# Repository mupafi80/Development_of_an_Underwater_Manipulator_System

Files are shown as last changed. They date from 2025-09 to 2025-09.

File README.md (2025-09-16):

# Development_of_an_Underwater_Manipulator_System
This repository documents the development of an underwater manipulator. It includes the design methodology, material selection for mechanical construction, electronic system components, software development, and the physical assembly of the manipulator. Design files for the manipulator arm components and electrical connection diagrams are available in this repository. This project is part of the doctoral thesis of PhD Salatiel García Nava.

The proposed arm structure and link dimensions are presented below.



The components of a link in the robotic arm, including sections of tubing, flanges, and seals, are observed.



Assembled links: the first one includes the o-rings between the threaded sections, while the lower two display the connecting threads.



García Nava, Salatiel (2025). Desarrollo de un brazo manipulador subacuático. Centro de Investigación y de Estudios Avanzados del IPN. Directores de tesis: Dr. Filiberto Muñoz Palacios, Dr. Sergio Rogelio Lozano Leal. Tesis de doctorado

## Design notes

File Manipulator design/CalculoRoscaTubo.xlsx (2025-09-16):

Calculo de las medidas básicas |  |  |  |  | Sistema ISO
Para el calculo de las distintas medidas se toman como base el diámetro exterior del tornillo d y el paso de rosca P.
Las roscas de este sistema son roscas métricas y sus medidas vienen expresadas en milímetros. El ángulo de rosca es de 60º.
 |  |  |  |  |  |  |  |  | Profundidad de rosca................. H = 0,866 · P
 |  |  |  |  |  |  |  |  | Altura de contacto....................... H1 = 0,541 · P
 |  |  |  |  |  |  |  |  | Altura del filete del tornillo...........h3 = 0,613 · P
 |  |  |  |  |  |  |  |  | Diámetro interior del tornillo.......d3 = d - 1,226 · P
 |  |  |  |  |  |  |  |  | Diámetro interior de la tuerca.....D1 = d - 1,082 · P
 |  |  |  |  |  |  |  |  | Diámetro medio...........................d2 = D2 = d - 0,649 · P
 |  |  |  |  |  |  |  |  | Diámetro exterior de la tuerca....D = d + 0,072 · P
 |  |  |  |  |  |  |  |  | Cálculo de d a partir de diametro de tubo …...............d=D1-(1.082*P) donde D1 es diametro interior de la tuerca
 | Diametro Nominal : |  | 51.418 |  | Paso: | 1 |  |  | DITuerca: | 52.4 | Paso: | 1 |  |  |  | Medida de redondo para hacer cuerda | 51.49
 |  |  |  |  |  |  |  |  |  |  |  |  |  |  |  | Medida de tubo para hacer cuerda | 52.4
 | H: | 0.866 | H1: | 0.541 | h3: | 0.613 |  |  | H: | 0.866 | H/8 | 0.10825 | H1 | 0.541 | d (new) | 53.482
 | d3: | 50.192 | D1: | 50.336 | d2=D2: | 50.769 | D: | 51.49 | 2H: | 1.732 | 2 H/8: | 0.2165 | d: | 53.482
 | Diametro Nominal : |  | 9.993 |  | Paso: | 1.5 |  |  | DITuerca: | 8.37 | Paso: | 1.5 |  |  |  | Medida de redondo para hacer cuerda | 10.101
 |  |  |  |  |  |  |  |  |  |  |  |  |  |  |  | Medida de tubo para hacer cuerda | 8.37
 | H: | 1.299 | H1: | 0.8115 | h3: | 0.9195 |  |  | H: | 1.299 | H/8 | 0.162375
 | d3: | 8.154 | D1: | 8.37 | d2=D2: | 9.0195 | D: | 10.101 | 2H: | 2.598 | 2 H/8: | 0.32475 | d: | 9.993
 |  |  |  |  |  |  |  |  | D1 | 50.407468
La Norma DIN 13-1, establece las características de las roscas métricas gruesas cuyos tamaños van desde la M1 a M68. En la Tabla B, como ejemplo se especifican los valores de algunas de ellas.
Diámetro nominal: D = d
Paso: P
D1 = d – 2·H1 = d – 1,082532·P
Diámetro medio: D2 = d2 = d – 0,649519 · P
Diámetro del núcleo: d3 = d – 1,226869 · P
H = 0,866025 · P
Profundidad portante de rosca: H1 = 0,541266·P
Profundidad de rosca: h3 = 0,613435·P
Radio fondo de rosca: R = H/6 = 0,144338 · P
Las roscas ISO métricas finas se regulan por la norma DIN 13-2 a la DIN 13-11 1999-11 y diámetros nominales de 1mm a 1000 mm y pasos finos de 0,2 a 8 mm.

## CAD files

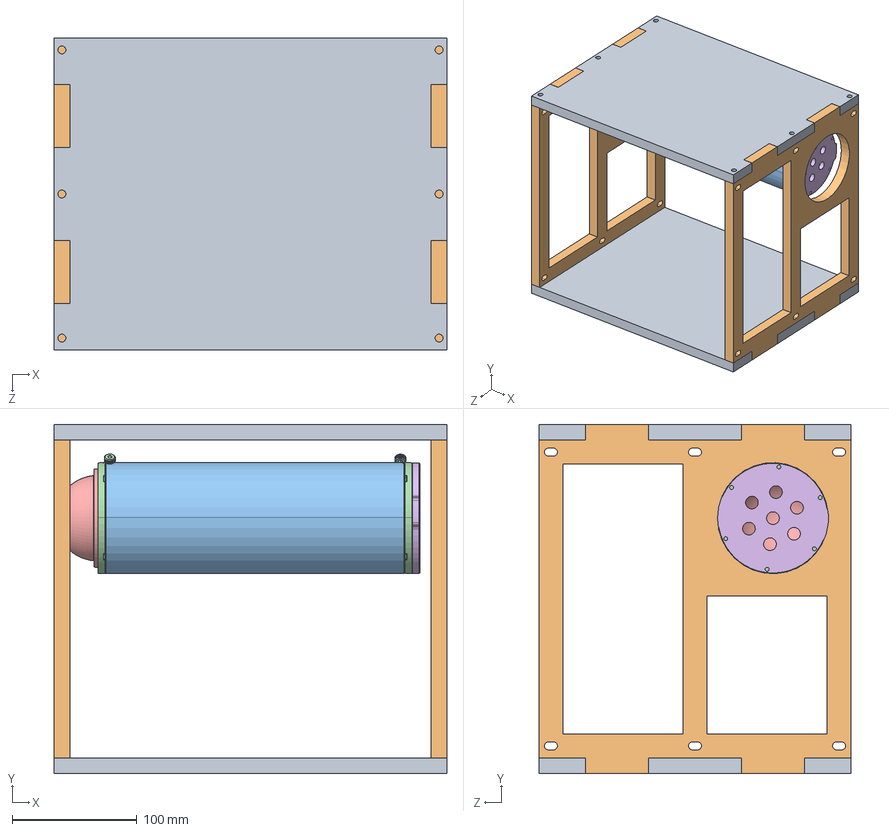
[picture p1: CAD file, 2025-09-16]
Manipulator design/EnsamblajeRobotC_Movimiento.SLDASM
315.0 x 280.0 x 250.0 mm
TP_Base x 2
Side_Base x 2
WTE3-P-LOCKING-TUBE-240-R2
WTE3-M-LOCKING-FLANGE-SEAL-R1-RP x 2
WTE3-P-DOME-R1
WTE3-M-END-CAP-7-HOLE-R1

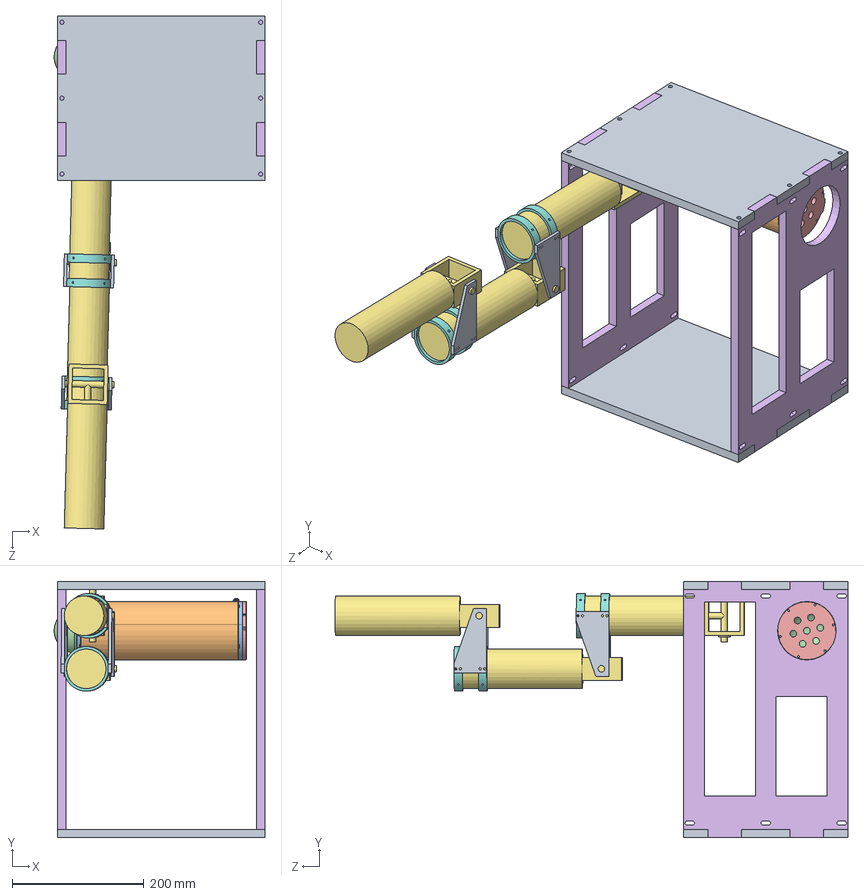
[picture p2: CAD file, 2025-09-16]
Manipulator design/EnsamblajeRobotC_Movimiento_Long.SLDASM
320.5 x 390.0 x 780.2 mm
TP_Base x 2
WTE3-P-LOCKING-TUBE-240-R2
WTE3-M-LOCKING-FLANGE-SEAL-R1-RP x 2
WTE3-P-DOME-R1
WTE3-M-END-CAP-7-HOLE-R1
Side_Base_Long x 2
EslabonSimplificado x 3
SujeccionMotorV2 x 4
Soporte x 4

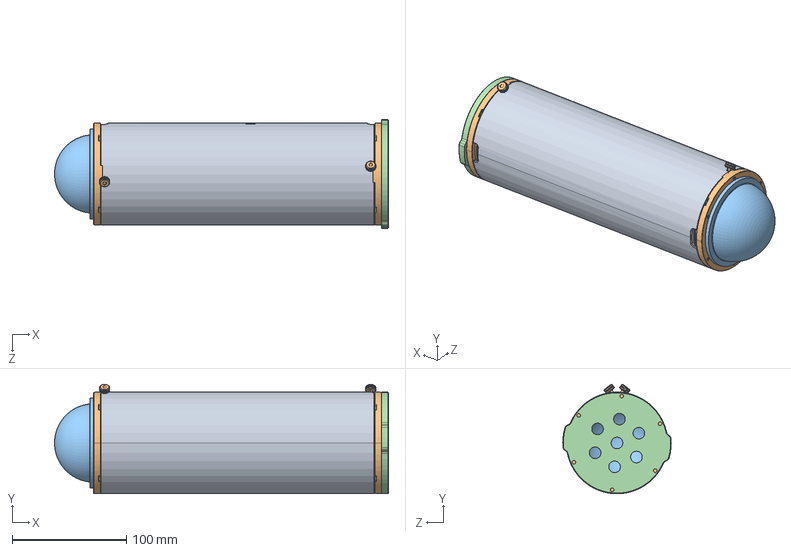
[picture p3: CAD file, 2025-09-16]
Manipulator design/tubo/EnsambleTubo.SLDASM
292.4 x 95.8 x 95.0 mm
WTE3-P-LOCKING-TUBE-240-R2
WTE3-M-LOCKING-FLANGE-SEAL-R1-RP x 2
WTE3-P-DOME-R1
WTE3-M-END-CAP-7-HOLE-R1

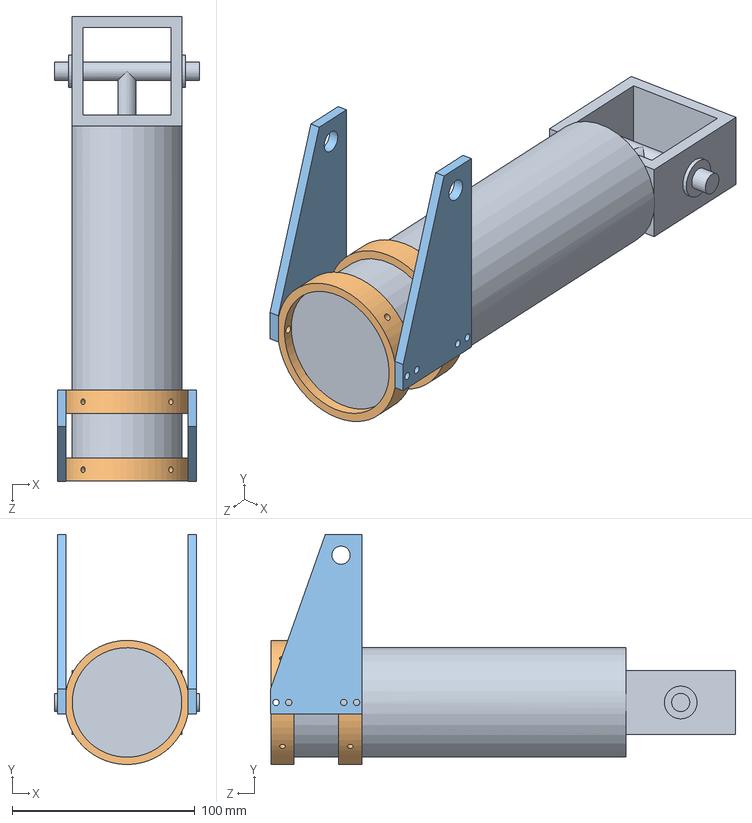
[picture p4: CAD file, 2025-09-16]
Manipulator design/EslabonHorizontal.SLDASM
79.5 x 126.0 x 254.6 mm
EslabonSimplificado
SujeccionMotorV2 x 2
Soporte x 2

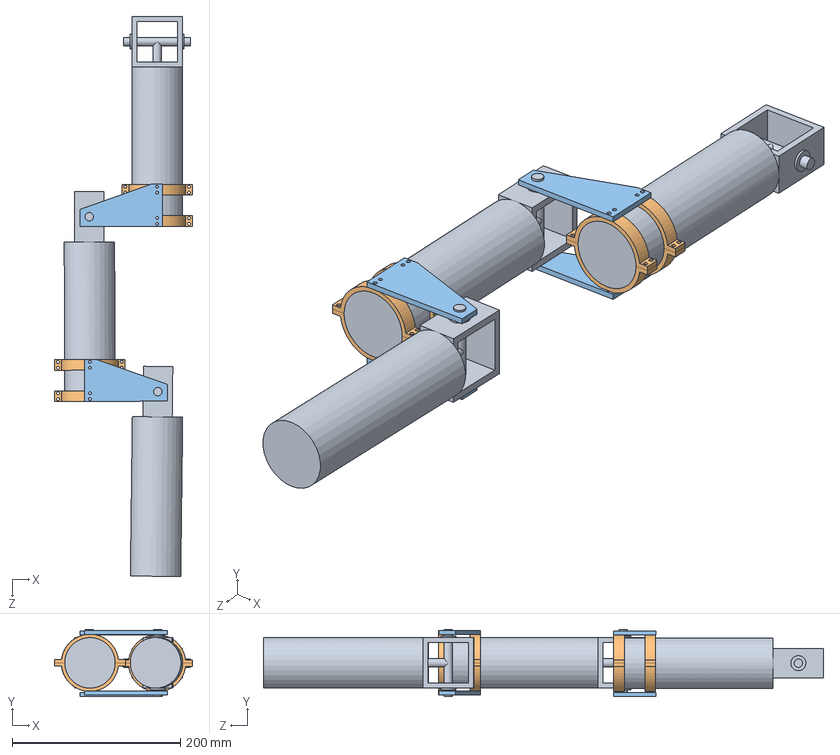
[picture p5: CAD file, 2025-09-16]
Manipulator design/EnsamblajeBrazo.SLDASM
164.0 x 79.9 x 665.9 mm
EslabonSimplificado x 3
SujeccionMotor x 8
Soporte x 4

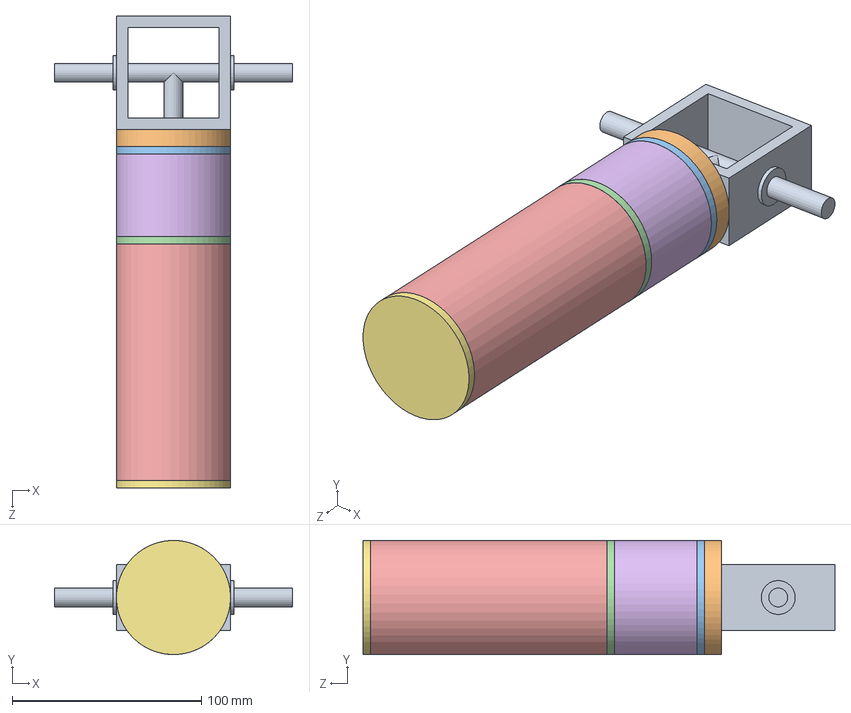
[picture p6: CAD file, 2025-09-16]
Manipulator design/EnsambleEslabonSimplificado.SLDASM
126.0 x 60.3 x 249.5 mm
GearBox
BridaGB
TapaBridaGB
BridaMotor
TuboMotor
TuboSello
TapaMotor

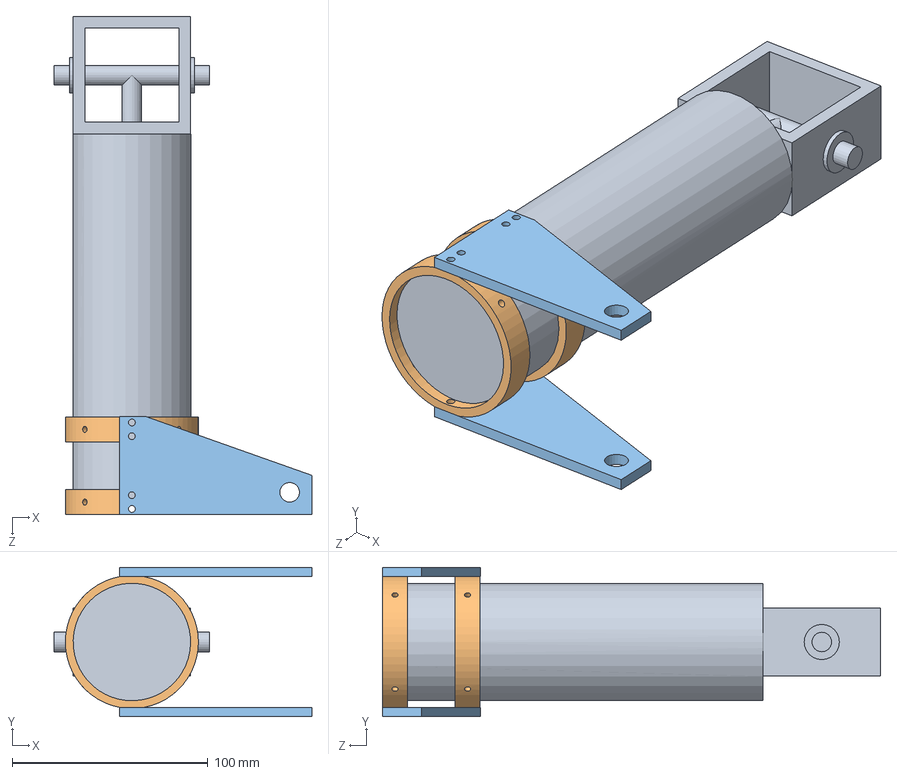
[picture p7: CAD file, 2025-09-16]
Manipulator design/EslabonVertical_Inv.SLDASM
131.8 x 76.3 x 254.5 mm
EslabonSimplificado
SujeccionMotorV2 x 2
Soporte x 2

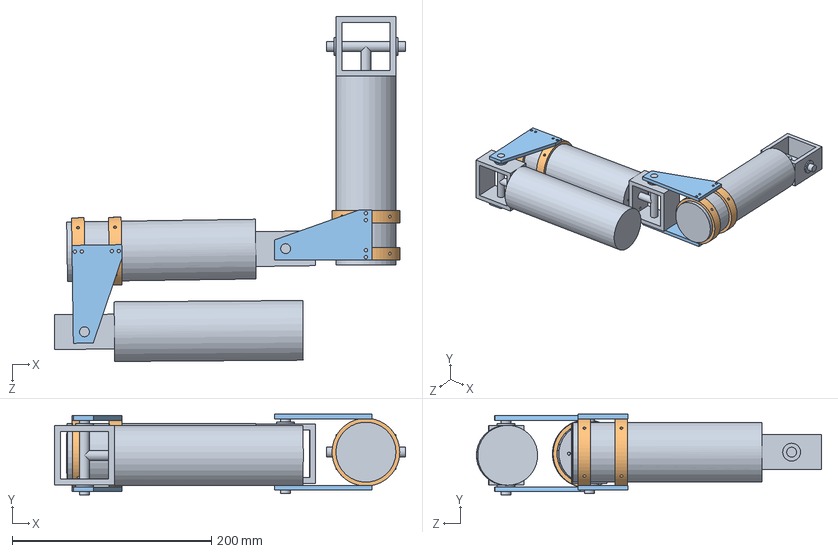
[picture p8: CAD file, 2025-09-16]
Manipulator design/EnsamblajeBrazoV2_2.SLDASM
352.5 x 81.1 x 346.5 mm
EslabonSimplificado x 3
SujeccionMotorV2 x 4
Soporte x 4

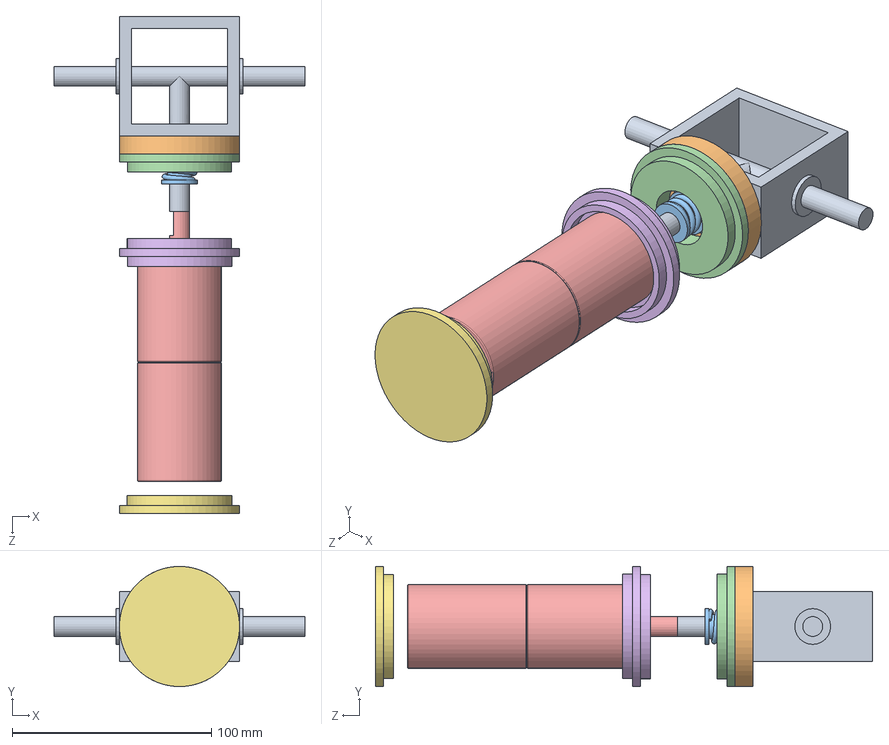
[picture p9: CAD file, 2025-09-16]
Manipulator design/EnsambleEslabon.SLDASM
126.0 x 60.3 x 249.5 mm
GearBox
BridaGB
Seal
TapaBridaGB
Motor9_7NM
BridaMotor
TapaMotor

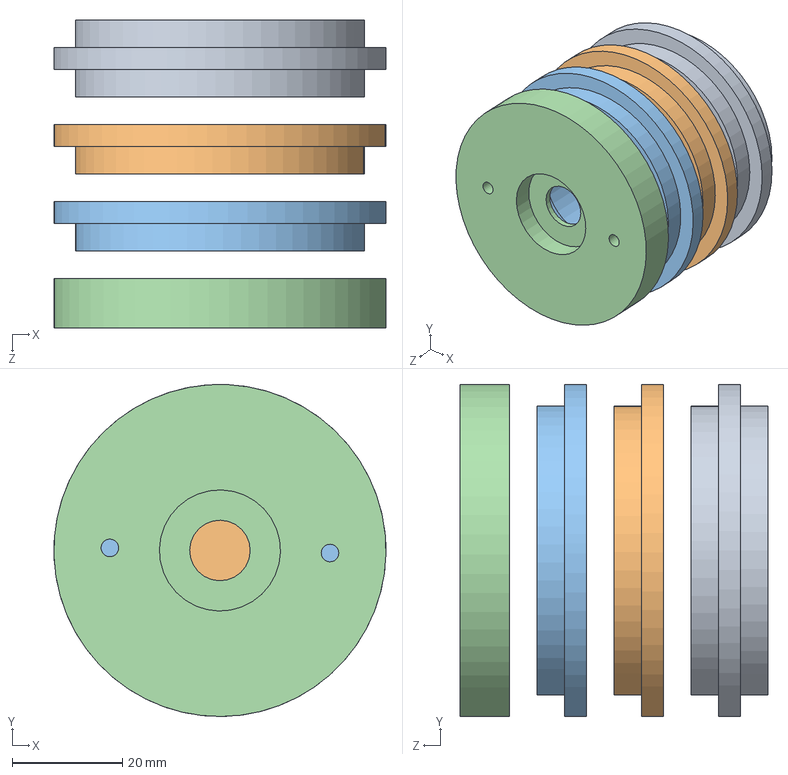
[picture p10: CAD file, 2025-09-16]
Manipulator design/EnsamblajeSeccionesBarra.SLDASM
60.3 x 60.3 x 56.0 mm
BridaMotor
TapaMotor
TapaBridaGB
BridaGB

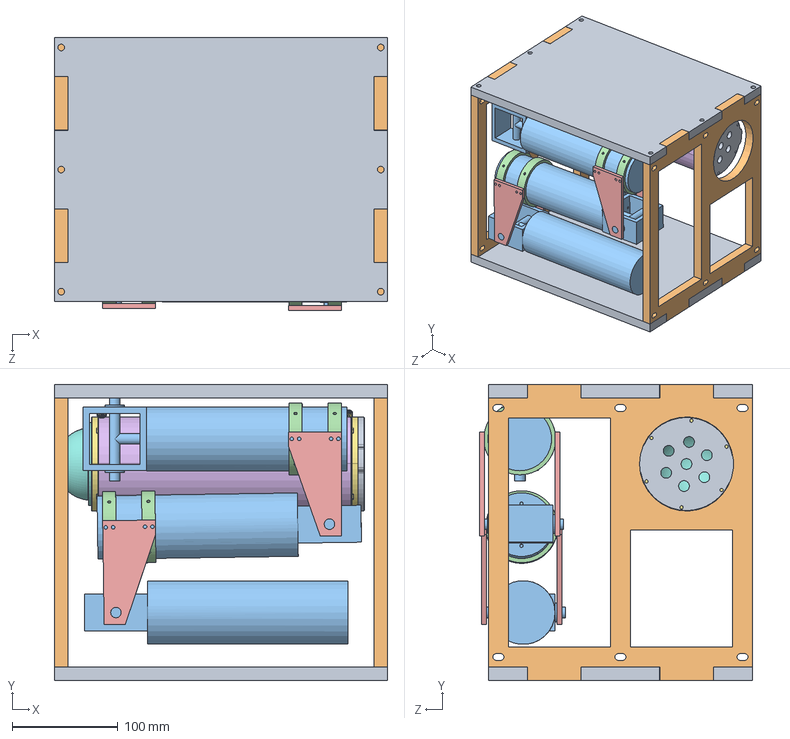
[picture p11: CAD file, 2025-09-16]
Manipulator design/EnsamblajeCompletoRobot.SLDASM
315.0 x 280.0 x 258.4 mm
TP_Base x 2
Side_Base x 2
EslabonSimplificado x 3
SujeccionMotorV2 x 4
Soporte x 4
WTE3-P-LOCKING-TUBE-240-R2
WTE3-M-LOCKING-FLANGE-SEAL-R1-RP x 2
WTE3-P-DOME-R1
WTE3-M-END-CAP-7-HOLE-R1

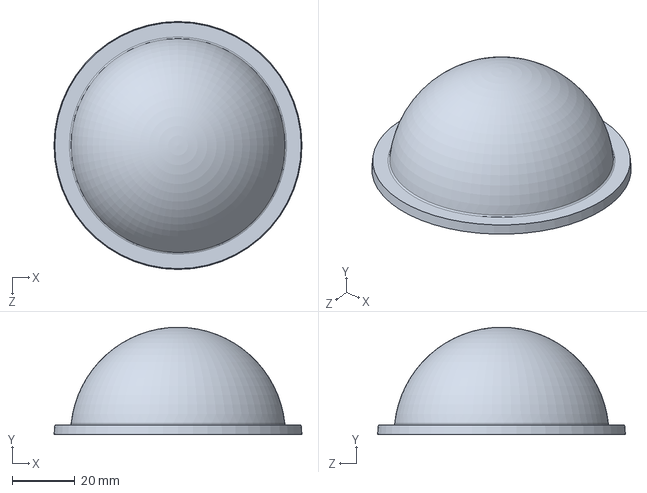
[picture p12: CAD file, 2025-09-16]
Manipulator design/tubo/WTE3-P-DOME-R1.SLDPRT
79.2 x 34.3 x 79.2 mm

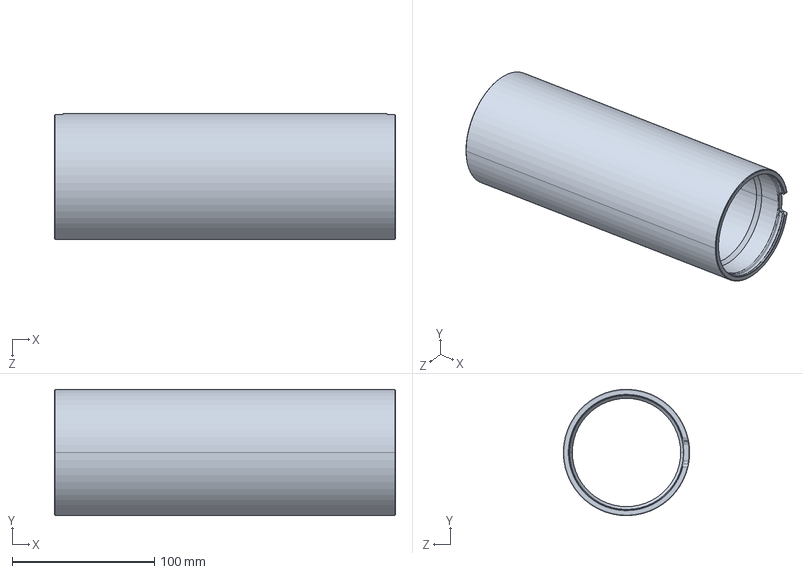
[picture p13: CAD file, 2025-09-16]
Manipulator design/tubo/WTE3-P-LOCKING-TUBE-240-R2.step
240.0 x 88.9 x 88.9 mm

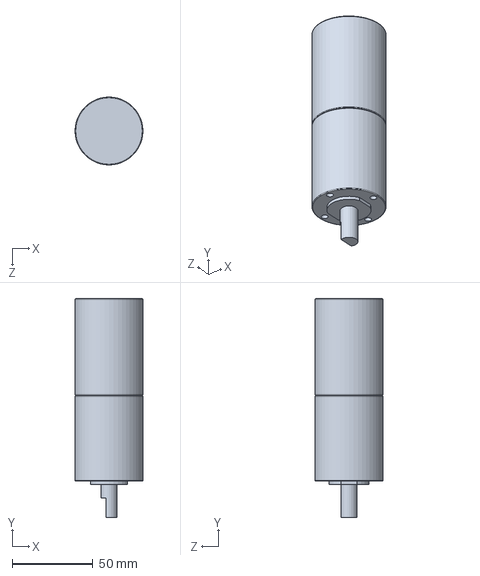
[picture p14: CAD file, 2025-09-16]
Manipulator design/Motor9_7NM.SLDPRT
42.0 x 135.5 x 42.0 mm

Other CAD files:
Manipulator design/EslabonVertical.SLDASM
Manipulator design/EslabonHorizontal_Inv.SLDASM
Manipulator design/tubo/WTE3-M-LOCKING-FLANGE-SEAL-R1-RP.SLDPRT
Manipulator design/BridaGB.SLDPRT
Manipulator design/BridaMotor.SLDPRT
Manipulator design/Cople.SLDPRT
Manipulator design/GearBox.SLDPRT
Manipulator design/Planos.SLDDRW
Manipulator design/Seal.SLDPRT
Manipulator design/Side_Base.DWG
Manipulator design/Side_Base.SLDPRT
Manipulator design/Side_Base_Long.DWG
Manipulator design/Side_Base_Long.SLDPRT
Manipulator design/Soporte.SLDPRT
Manipulator design/Soporte.STL
Manipulator design/SujeccionMotor.SLDPRT
Manipulator design/SujeccionMotorV2.SLDDRW
Manipulator design/SujeccionMotorV2.SLDPRT
Manipulator design/SujeccionMotorV2.STL
Manipulator design/SujeccionMotorV2_2.STL
Manipulator design/TP_Base.DWG
Manipulator design/TP_Base.SLDPRT
Manipulator design/TapaBridaGB.SLDPRT
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

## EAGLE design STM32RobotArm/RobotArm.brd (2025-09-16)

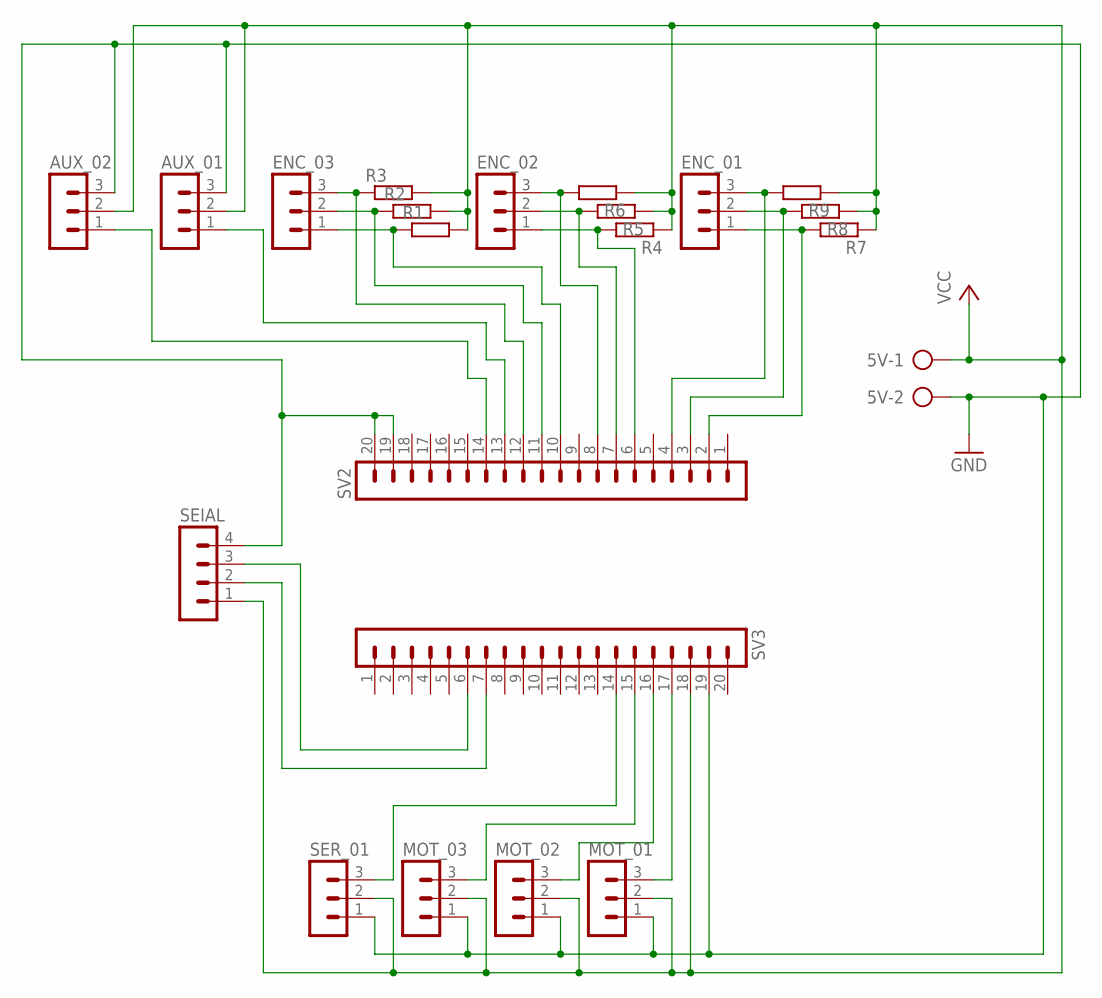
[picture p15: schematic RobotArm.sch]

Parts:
5V: AK500/2-H
AUX_01, AUX_02: MA03-1
ENC_01, ENC_02, ENC_03: MA03-1
MOT_01, MOT_02, MOT_03: MA03-1
R1, R2, R3, R4, R5, R6, R7, R8, R9: R-EU_0207/10; 0207/10
SEIAL: MA04-1
SER_01: MA03-1
SV2, SV3: MA20-1

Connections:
GND: 5V.2, AUX_01.3, AUX_02.3, MOT_01.1, MOT_02.1, MOT_03.1, SEIAL.4, SER_01.1, SV2.19, SV2.20, SV3.19
unnamed: ENC_01.3, R9.2, SV2.4
unnamed: ENC_01.2, R8.2, SV2.3
unnamed: ENC_01.1, R7.2, SV2.2
unnamed: ENC_02.3, R6.2, SV2.8
unnamed: ENC_02.2, R5.2, SV2.7
unnamed: ENC_02.1, R4.2, SV2.6
unnamed: ENC_03.3, R3.1, SV2.12
unnamed: ENC_03.2, R2.1, SV2.11
unnamed: ENC_03.1, R1.1, SV2.10
unnamed: AUX_01.1, SV2.13
unnamed: AUX_02.1, SV2.14
unnamed: MOT_01.3, SV3.17
unnamed: MOT_02.3, SV3.16
unnamed: MOT_03.3, SV3.15
unnamed: SER_01.3, SV3.14
unnamed: SEIAL.2, SV3.7
unnamed: SEIAL.3, SV3.6
VCC: 5V.1, AUX_01.2, AUX_02.2, MOT_01.2, MOT_02.2, MOT_03.2, R1.2, R2.2, R3.2, R4.1, R5.1, R6.1, R7.1, R8.1, R9.1, SEIAL.1, SER_01.2, SV3.18

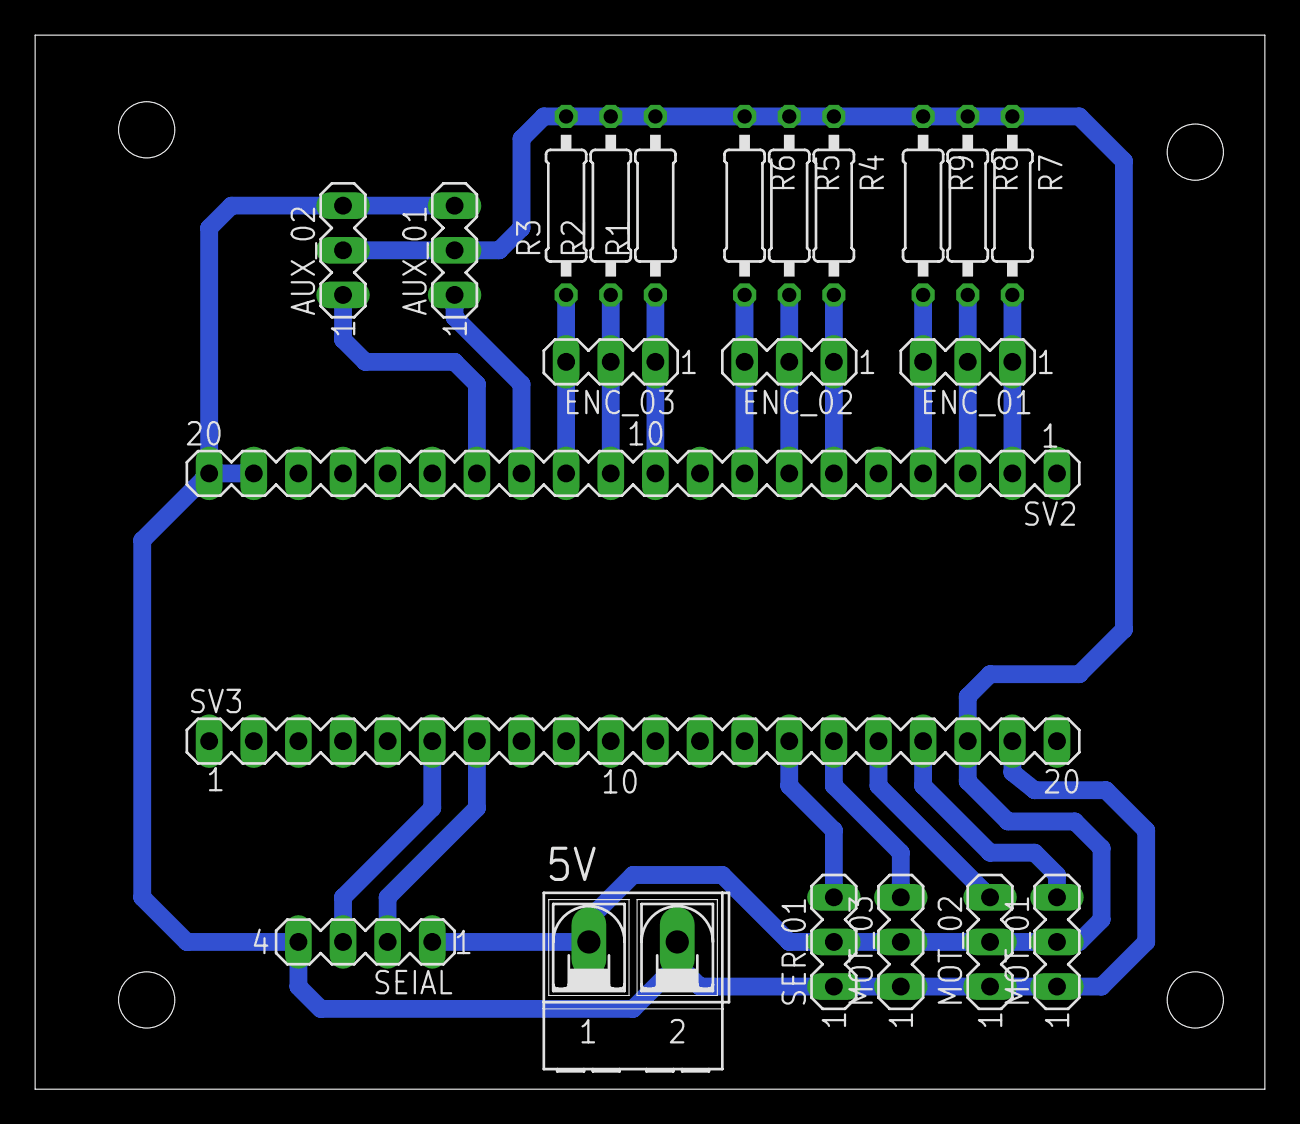
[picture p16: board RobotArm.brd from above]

Board: 2 copper layers, 70.0 x 60.0 mm, 22 parts (0 on the bottom side), 19 nets.

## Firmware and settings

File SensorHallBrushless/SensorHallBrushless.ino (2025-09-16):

//INTERRUPTS IN STM32F103C8
#include <Servo.h>
Servo PWM1;  //3.NM
Servo PWM2;  //6.9NM
Servo PWM3;  //9.7NM

//Motor 1 par 3.4 NM
const int AA1 = PA5; // Entrada de la señal A del encoder.
const int BB1 = PA6; // Entrada de la señal B del encoder.
const int CC1 = PA7; // Entrada de la señal C del encoder.

//Motor 1 par 6.9 NM
const int AA2 = PC13; // Entrada del encoder.
const int BB2 = PC14; 
const int CC2 = PC15; 

//Motor 1 par 9.7 NM
const int AA3 = PA1; // Entrada del encoder.
const int BB3 = PA2; 
const int CC3 = PA3; 

volatile int  n1 = 0, n2 = 0,n3 = 0 ;
volatile byte ant1 = 0, ant2 = 0, ant3 = 0;
volatile byte act1 = 0, act2 = 0, act3 = 0;

float grados1 = 0.0, grados1_ant=0.0, vel1=0.0, int_grados1=0.0;
float grados2 = 0.0, grados2_ant=0.0, vel2=0.0, int_grados2=0.0;
float grados3 = 0.0, grados3_ant=0.0, vel3=0.0, int_grados3=0.0;

float pos_des1=-90, pid1=0.0, e1=0.0, e1_p=0.0, e1_i=0.0;
float pos_des2=-90, pid2=0.0, e2=0.0, e2_p=0.0, e2_i=0.0;
float pos_des3=-90, pid3=0.0, e3=0.0, e3_p=0.0, e3_i=0.0;

float kp1 = 3.4, kd1 = 1.0, ki1 = 1.0;
float kp2 = 3.5, kd2 = 1.0, ki2 = 1.0;
float kp3 = 3.5, kd3 = 1.0, ki3 = 1.0;

//int pwm1 = 0; 

unsigned long lastTime = 0;  // Tiempo anterior
unsigned long sampleTime = 50;  // Tiempo de muestreo

float offset(float d);

void setup()
{
  Serial.begin(9600);

  pinMode(AA1, INPUT);
  pinMode(BB1, INPUT);
  pinMode(CC1, INPUT);
  pinMode(AA2, INPUT);
  pinMode(BB2, INPUT);
  pinMode(CC2, INPUT);
  pinMode(AA3, INPUT);
  pinMode(BB3, INPUT);
  pinMode(CC3, INPUT);

  PWM1.attach(PB7,1000,2000); // pin, min input ms, max input ms
  PWM2.attach(PB8,1000,2000);
  PWM3.attach(PB9,1000,2000);

  PWM1.write(90);
  PWM2.write(90);
  PWM3.write(90);

  //3.4NM
  attachInterrupt(digitalPinToInterrupt(AA1), encoder1, CHANGE);
  attachInterrupt(digitalPinToInterrupt(BB1), encoder1, CHANGE);
  attachInterrupt(digitalPinToInterrupt(CC1), encoder1, CHANGE);

  //6.9NM
  attachInterrupt(digitalPinToInterrupt(AA2), encoder2, CHANGE);
  attachInterrupt(digitalPinToInterrupt(BB2), encoder2, CHANGE);
  attachInterrupt(digitalPinToInterrupt(CC2), encoder2, CHANGE);

  //9.7NM
  attachInterrupt(digitalPinToInterrupt(AA3), encoder3, CHANGE);
  attachInterrupt(digitalPinToInterrupt(BB3), encoder3, CHANGE);
  attachInterrupt(digitalPinToInterrupt(CC3), encoder3, CHANGE);
  
  //Serial.println("Numero de conteos");
  delay(2000);
}

void loop() {
  grados1 = n1*0.1787;  //deg  2014
  grados2 = n2*0.0708;  //deg  5085
  grados3 = n3*0.0507;  //deg  7098

//Serial.print(" n2  6.9 ");Serial.print(grados2);  //debug
//Serial.print(" n3  9.7 ");Serial.println(grados3);  //debug
  
  if (millis() - lastTime >= sampleTime || lastTime==0)
  {  // Se actualiza cada sampleTime (milisegundos)
      lastTime = millis();
      
      vel1 = (grados1 - grados1_ant)/0.05; //deg-s
      int_grados1 = int_grados1+(grados1*0.05); //deg s
      e1 = pos_des1 - grados1;
      e1_p = 0 - vel1;
      e1_i = 0 - int_grados1;

      pid1 = -(kp1*e1 + kd1*e1_p);// + ki1*e1_i;
      PWM1.write(offset(pid1));

      vel2 = (grados2 - grados2_ant)/0.05; //deg-s
      int_grados2 = int_grados2+(grados2*0.05); //deg s
      e2 = pos_des2 - grados2;
      e2_p = 0 - vel2;
      e2_i = 0 - int_grados2;

      pid2 = -(kp2*e2 + kd2*e2_p);// + ki1*e1_i;
      PWM2.write(offset(pid2));

      vel3 = (grados3 - grados3_ant)/0.05; //deg-s
      int_grados3 = int_grados3+(grados3*0.05); //deg s
      e3 = pos_des3 - grados3;
      e3_p = 0 - vel3;
      e3_i = 0 - int_grados3;

      pid3 = (kp3*e3 + kd3*e3_p);// + ki1*e1_i;
      PWM3.write(offset(pid3));

      
//      Serial.print(" e: ");Serial.print(e3);  //debug
//      Serial.print(" pid: ");Serial.print(pid3);  //debug
//      Serial.print(" pid_offset: ");Serial.println(offset(pid3));  //debug
      
      
      //Actualiza variables
      grados1_ant = grados1;
      grados2_ant = grados2;
      grados3_ant = grados3;

      //Monitor 
//      Serial.print(" pose deg: ");Serial.print(grados1);
//      Serial.print(" derivate: ");Serial.print(vel1);
//      Serial.print(" integral: ");Serial.println(int_grados1);
   }
   
}

// Encoder 3 fases.
void encoder1(void)
{
  ant1=act1;
  
  if(digitalRead(AA1)) bitSet(act1,2); else bitClear(act1,2);            
  if(digitalRead(BB1)) bitSet(act1,1); else bitClear(act1,1);
  if(digitalRead(CC1)) bitSet(act1,0); else bitClear(act1,0);
      
  if(ant1 == 1 && act1 ==5) n1++;
  if(ant1 == 3 && act1 ==1) n1++;
  if(ant1 == 2 && act1 ==3) n1++;
  if(ant1 == 6 && act1 ==2) n1++;
  if(ant1 == 4 && act1 ==6) n1++;
  if(ant1 == 5 && act1 ==4) n1++;
  
  if(ant1 == 1 && act1 ==3) n1--;
  if(ant1 == 3 && act1 ==2) n1--;
  if(ant1 == 2 && act1 ==6) n1--;
  if(ant1 == 6 && act1 ==4) n1--;
  if(ant1 == 4 && act1 ==5) n1--;
  if(ant1 == 5 && act1 ==1) n1--;    

//  Serial.print(" A: ");Serial.print(digitalRead(AA1));  //DEBUG
//  Serial.print(" B: ");Serial.print(digitalRead(BB1));
//  Serial.print(" C: ");Serial.print(digitalRead(CC1));
//  Serial.print(" ESTADO: ");Serial.println(act1);
}

void encoder2(void)
{
  ant2=act2;
  
  if(digitalRead(AA2)) bitSet(act2,2); else bitClear(act2,2);            
  if(digitalRead(BB2)) bitSet(act2,1); else bitClear(act2,1);
  if(digitalRead(CC2)) bitSet(act2,0); else bitClear(act2,0);
    
  if(ant2 == 1 && act2 ==5) n2++;
  if(ant2 == 3 && act2 ==1) n2++;
  if(ant2 == 2 && act2 ==3) n2++;
  if(ant2 == 6 && act2 ==2) n2++;
  if(ant2 == 4 && act2 ==6) n2++;
  if(ant2 == 5 && act2 ==4) n2++;
  
  if(ant2 == 1 && act2 ==3) n2--;
  if(ant2 == 3 && act2 ==2) n2--;
  if(ant2 == 2 && act2 ==6) n2--;
  if(ant2 == 6 && act2 ==4) n2--;
  if(ant2 == 4 && act2 ==5) n2--;
  if(ant2 == 5 && act2 ==1) n2--;    
}

void encoder3(void)
{
  ant3=act3;
  
  if(digitalRead(AA3)) bitSet(act3,2); else bitClear(act3,2);            
  if(digitalRead(BB3)) bitSet(act3,1); else bitClear(act3,1);
  if(digitalRead(CC3)) bitSet(act3,0); else bitClear(act3,0);
    
  if(ant3 == 1 && act3 ==5) n3++;
  if(ant3 == 3 && act3 ==1) n3++;
  if(ant3 == 2 && act3 ==3) n3++;
  if(ant3 == 6 && act3 ==2) n3++;
  if(ant3 == 4 && act3 ==6) n3++;
  if(ant3 == 5 && act3 ==4) n3++;
  
  if(ant3 == 1 && act3 ==3) n3--;
  if(ant3 == 3 && act3 ==2) n3--;
  if(ant3 == 2 && act3 ==6) n3--;
  if(ant3 == 6 && act3 ==4) n3--;
  if(ant3 == 4 && act3 ==5) n3--;
  if(ant3 == 5 && act3 ==1) n3--;    
}


float offset(float d)  //pwm 0 - 65 535 middle  32768 
{
  float out;
  if(d >= 0)
  {
    out = (90+d);
    if (out > 180) out=180;
    return out;
  }
  else if(d  < 0)
  {    
    out = (90+d);
    if (out < 0) out=0;
    return out;
  }

  
}
  

////PRUEBA BIT SET
//int x = 0b00000111;
//int n = 0;  ///Posicion del bit que cambia
//  
//void setup() {
//  Serial.begin(9600);
//  while (!Serial) {
//    ; // wait for serial port to connect. Needed for native USB port only
//  }
//
//  
//}
//
//void loop() {
//  bitClear(x,0);
//  Serial.println(x); // print the output of bitSet(x,n)
//  delay(500);
//  bitClear(x,1);
//  Serial.println(x); // print the output of bitSet(x,n)
//  delay(500);
//}
